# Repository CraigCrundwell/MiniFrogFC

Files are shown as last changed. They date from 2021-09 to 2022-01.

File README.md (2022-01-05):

# MiniFrogFC
A Flight Controller For Brushed Motor Quadcopters <br /> <br />

## About
This is a personal project to develop a custom PCB flight controller designed in Altium. The size is currently 27mm x 18mm which is smaller than many commercially available options :) 
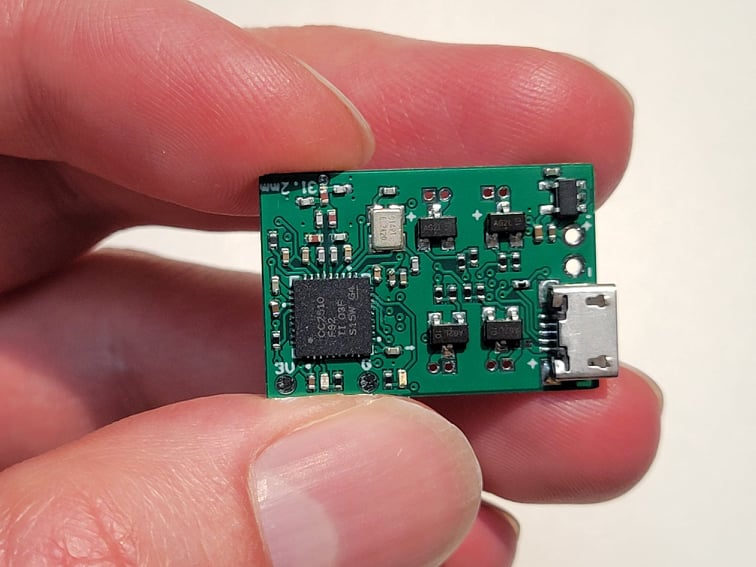
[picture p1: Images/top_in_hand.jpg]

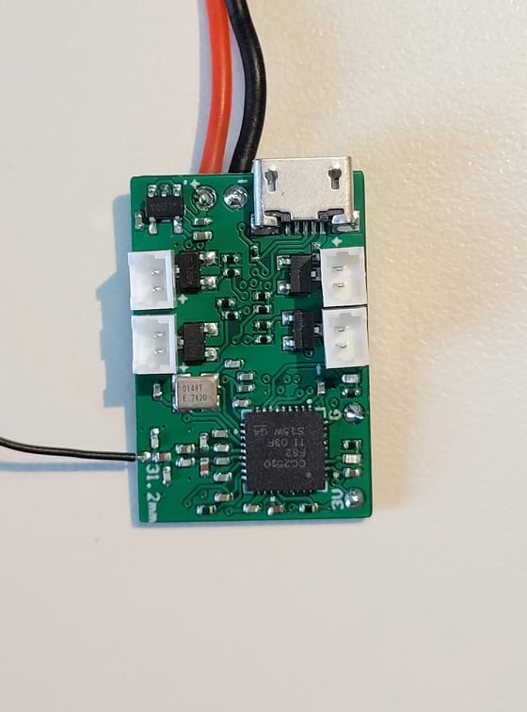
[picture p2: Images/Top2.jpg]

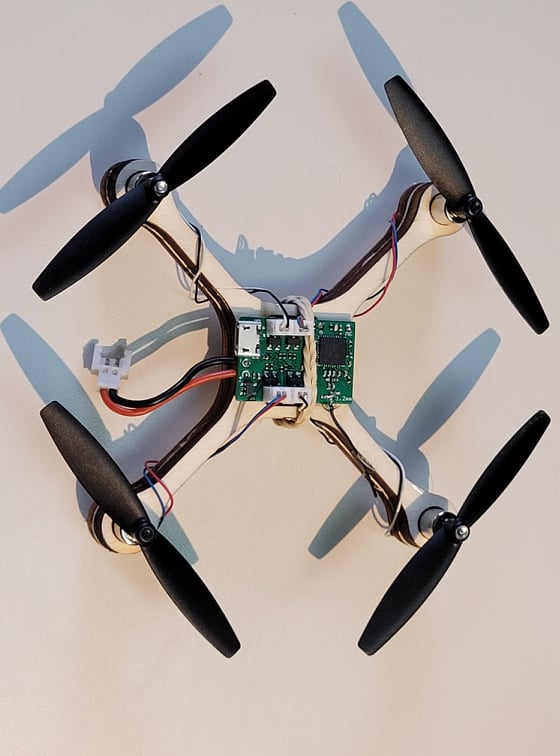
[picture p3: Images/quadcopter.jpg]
Quadcopter


## Major Components

**STM32F303CCT6:** F3 microcontroller <br />
**CC2510F32RHHR:** RF microcontroller for integrated FrSky receiver <br />
**MPU-6050:** Gyroscope and accelerometer IC <br />

## FrSky Compatability
The built in FrSky compatible receiver is based off the [uSky](https://github.com/fishpepper/uSKY) receiver design 
running [OpenSky](https://github.com/fishpepper/OpenSky) firmware developed by [fishpepper.](https://github.com/fishpepper) <br />
Thanks to fishpepper for publishing the design under an opensource license! 

## BetaFlight Compatibility

This flight controller is designed to be compatible with a popular open source FC software program called [BetaFlight.](https://github.com/betaflight) 
I have developed a new target for this custom flight controller here: [MiniFrogFC_Betaflight](https://github.com/CraigCrundwell/MiniFrogFC_Betaflight) <br />
Thanks to the BetaFlight team for their incredible work! <br />

**Note:** BetaFlight 4.0.6 is the last version that supports F3 based flight controllers. This custom target can not be built on newer versions! <br />

## The MiniFrogFC Name
I think frogs are neat... <br />
Other flight controllers have creative names much better than my original "Brushed Quadcopter FC." <br />
This name is one of a few I thought of in 5 minutes that didn't return strange results when entered on Google. <br />
Meh, we are just going to roll with it. 

## Versions

The V1.0 board layout is complete and fully tested.

## PCB Build Notes  
1. Measure the antenna from a thin flexible wire as close to 32.2mm as possible with a ruler
2. The flight controller should be powered with a battery when plugged into USB only if R9 is not populated. Otherwise, don’t plug in the battery at the same time as the USB. 

## Receiver Flashing  
1.	Disconnect the USB and battery from the flight controller so that only the CC Debugger will power the flight controller.
2.	Solder wires onto the GND, 3V, CLK, DATA, and RESET pads on the flight controller labelled G, 3V, D, C, and R respectively. Connect the wires from the flight controller to the plug on the ribbon cable as shown below. Note the notch on the left side of the CC Debugger ribbon cable plug is shown in the drawing for orientation.  
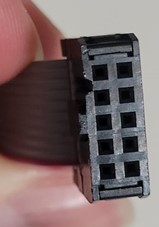
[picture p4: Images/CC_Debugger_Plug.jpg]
Plug

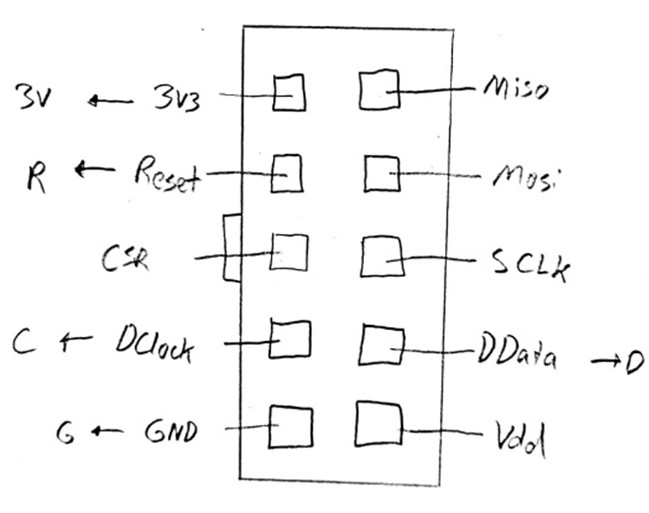
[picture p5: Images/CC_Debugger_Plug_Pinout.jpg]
Pinout
  
3.	Connect the CC Debugger USB to the computer. Make sure CC debugger drivers are installed first and that it shows up in device manager under "cebal controller devices"  
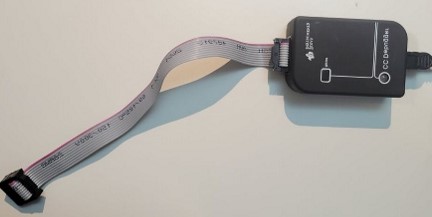
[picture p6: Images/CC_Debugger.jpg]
Debugger
  
5.	With the CC Debugger plugged in and the 5 wires connected to the flight controller, press the reset button on the CC Debugger. If everything is correct the light should turn green on the debugger. 
6.	Get the compiled hex file eg “MiniFrogFC_Receiver_binary_PPM” from the firmware folder

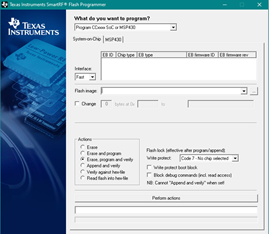
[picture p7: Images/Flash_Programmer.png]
Flasher
  
  
7.	(In windows) open Texas Instruments “Smart RF Flash Programmer”  
8.	Browse to the compiled hex file under “flash image”
9.	Click “perform actions” to flash the binary

## Receiver Binding  
1.	On a FrSky compatible transmitter, configure a model with international D8 mode.
2.	Power the flight controller while shorting the data pad “D” to GND “G”.
3.	Hold the transmitter about a meter away and enter bind mode. 
4.	Power cycle the flight controller. 

## Betaflight Target Flashing
1.	Power the flight controller while shorting the pads of the unplaced resistor R15 in the image below. This places the flight controller in DFU mode.  
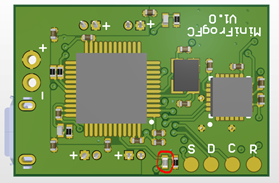
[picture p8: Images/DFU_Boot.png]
DFU_boot
 
2.	On Betaflight go to the flashing page and make sure the “No Reboot Sequence” and “Full Chip Erase” are selected.
3.	Select “Load Firmware [Local]” and browse to the binary file eg “betaflight_4.0.6_MINIFROG_FC.hex”.
4.	Flash the firmware then power cycle the flight controller.
5.	The flight controller should now show up as a USB port when plugged in. 

## Betaflight Configuration (Instructions for configurator version 10.7.0)
1.	Under configurations tab, set the board and sensor alignment to 180-degree roll and 90-degree yaw.
2.	Set the gyro update frequency to a maximum of 4.00 kHz and the PID loop frequency to 2.00 kHz.
3.	Set the receiver to PPM RX input in the configuration tab, and ensure the channel mapping is correct in the receiver tab.
4.	Set the ESC/Motor to Brushed with 32000 motor PWM frequency. 
5.	Set the PIDs as shown below. Note these will need to be adjusted for different quadcopter builds but they are a good starting point for 7mm brushed builds. 
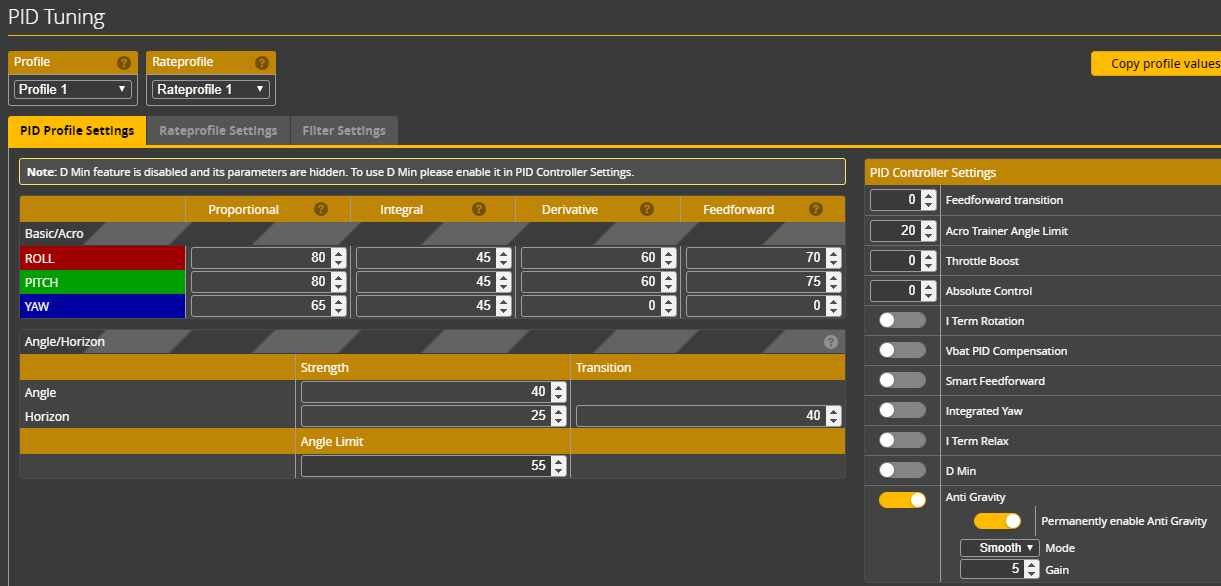
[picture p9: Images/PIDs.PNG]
PIDs
 
6.	Set the modes for acro, horizon, airmode, etc.
7.	Turn off blackbox logging, and disable permanent airmode.
8.	Be sure to save and reboot where necessary. 
9.	FLY!

## Improvements  
1.	Add a diode to allow for the battery and USB to be connected at once
2.	Add a voltage divider connection to the STM32 from the battery to monitor the voltage
3.	Add polarity markings to the LED footprints silkscreen
4.	Add an arrow for flight controller mounting orientation

# Advanced Development Notes 

## Basic outline to build a receiver binary:
1.	Download the USKY github repo on linux
2.	sudo apt-get install sdcc
3.	sudo apt-get install srecord
4.	If there is an error for python not found on make:  
  a.	sudo apt-get install python2-minimal  
  b.	cd /usr/bin  
  c.	sudo ln -s /usr/bin/python2.7 /usr/bin/python  
5.	In the USKY repo run:  
  a.	export TARGET=USky  
  b.	make  
  
  ## Basic notes on Betaflight configurator use in Linux:
To fix error: "Are udev rules installed correctly? See docs for instructions" when flashing firmware open terminal and enter:  

(echo '# DFU (Internal bootloader for STM32 MCUs)'; echo 'SUBSYSTEM=="usb", ATTRS{idVendor}=="0483", ATTRS{idProduct}=="df11", MODE="0664", GROUP="plugdev"') | sudo tee     /etc/udev/rules.d/45-stdfu-permissions.rules > /dev/null^C  

 then replace <username> with computer user name and enter:  
 sudo usermod -a -G plugdev <username>  

To resolve error of unable to connect to a flashed board, replace <username> with computer user name and enter:  
sudo usermod -a -G dialout <username>

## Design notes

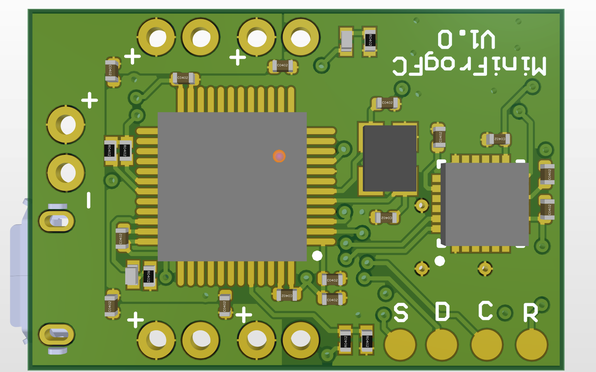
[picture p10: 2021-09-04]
Images/Top.png

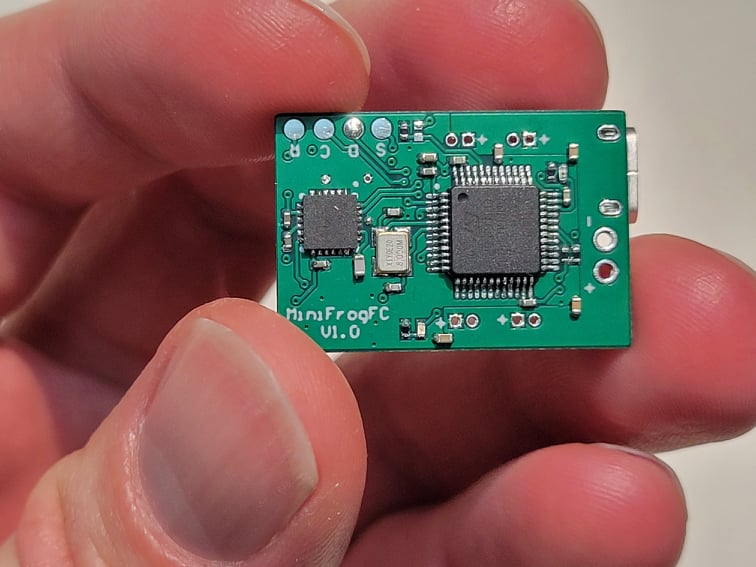
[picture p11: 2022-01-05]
Images/bottom_in_hand.jpg

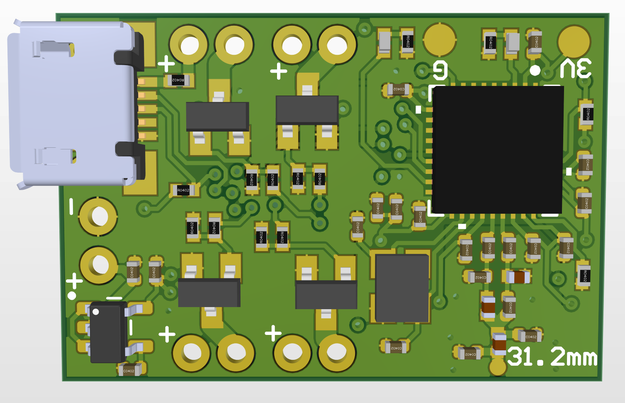
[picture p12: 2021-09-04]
Images/Bottom.png

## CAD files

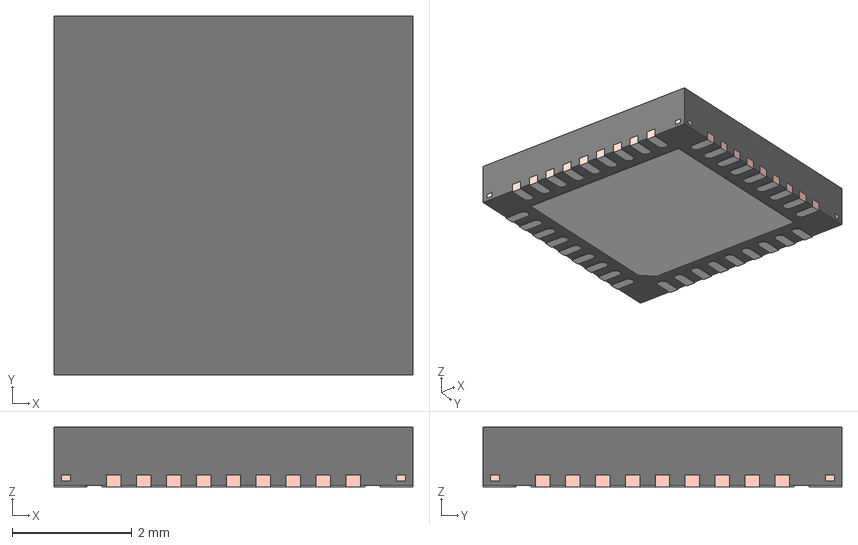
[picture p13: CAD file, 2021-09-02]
Components/3D Models/CC2510F16RHHR.stp
6.00 x 6.00 x 1.00 mm
FRAME
PIN1_AREA

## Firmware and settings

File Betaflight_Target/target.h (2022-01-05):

/*
 * This file is part of Cleanflight and Betaflight.
 *
 * Cleanflight and Betaflight are free software. You can redistribute
 * this software and/or modify this software under the terms of the
 * GNU General Public License as published by the Free Software
 * Foundation, either version 3 of the License, or (at your option)
 * any later version.
 *
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
 * If not, see <http://www.gnu.org/licenses/>.
 */

#pragma once

#define TARGET_BOARD_IDENTIFIER "MFRG"
#define USE_TARGET_CONFIG
#define BRUSHED_MOTORS

#define LED0_PIN                PA13
#define LED1_PIN                PC14

#define USE_GYRO
#define USE_GYRO_MPU6050
#define GYRO_1_ALIGN            CW0_DEG

#define USE_ACC
#define USE_ACC_MPU6050
#define ACC_1_ALIGN             CW0_DEG

#define USE_VCP
#define USE_UART1
#define USE_UART2

#define SERIAL_PORT_COUNT       2

#define USE_ESCSERIAL
#define ESCSERIAL_TIMER_TX_PIN  PA15

#define UART1_TX_PIN            PA9
#define UART1_RX_PIN            PA10

#define UART2_TX_PIN            PA14 
#define UART2_RX_PIN            PA15

#define USE_I2C
#define USE_I2C_DEVICE_2
#define I2C_DEVICE              (I2CDEV_2)


#define DEFAULT_RX_FEATURE      FEATURE_RX_PPM
#define DEFAULT_FEATURES        (FEATURE_TELEMETRY)

// IO - stm32f303cc in 48pin package
#define TARGET_IO_PORTA         0xffff
#define TARGET_IO_PORTB         0xffff
#define TARGET_IO_PORTC         (BIT(13)|BIT(14)|BIT(15))
#define TARGET_IO_PORTF         (BIT(0)|BIT(1)|BIT(4))

#define USABLE_TIMER_CHANNEL_COUNT 8
#define USED_TIMERS             (TIM_N(1) | TIM_N(2) | TIM_N(4) | TIM_N(8) | TIM_N(15))

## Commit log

2021-09-02 Added initial files
    [CC2510F16RHHR.PcbLib, CC2510F16RHHR.SchLib, CC2510F16RHHR.stp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]
2021-09-03 Started layout of FC PCB
2021-09-04 Layout of v1.0 board done
    [MiniFrogFC_lib.PcbLib, MiniFrogFC_v1.PcbDoc, MiniFrogFC_v1.PrjPcb]
2021-11-19 Added motor connectors
    [MCU.SchDoc, MiniFrogFC_lib.PcbLib, MiniFrogFC_lib.SchLib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]
2021-11-24 Production files added
    [MiniFrogFC_v1.PcbDoc, MiniFrogFC_v1.PrjPcb]
2022-01-05 V1 assembled and flown. Improved documentation.
    [IMU.SchDoc, MCU.SchDoc, MiniFrogFC_v1.PcbDoc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]
